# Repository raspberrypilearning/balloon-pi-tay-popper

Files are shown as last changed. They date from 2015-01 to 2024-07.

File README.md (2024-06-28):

# Balloon Pi-tay popper

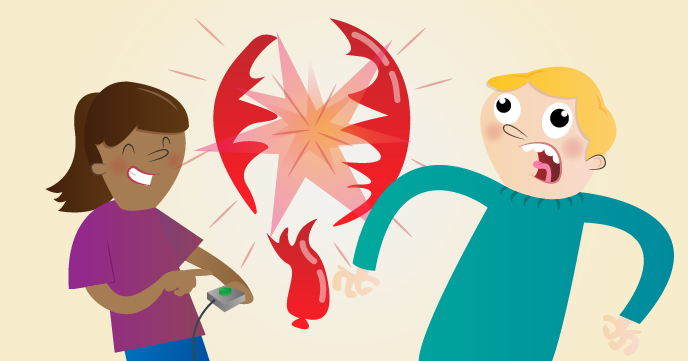
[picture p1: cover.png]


To pop balloons you might usually use a pin. Here you’ll be doing the same, but using a GPIO pin on your Raspberry Pi, not the pin you might be thinking of!

## Requirements

As well as a Raspberry Pi with an SD card loaded with Raspbian, you'll also need:

### Hardware

- 1 x Solderless breadboard
- 4 x Pin-to-socket jumper leads
- 7 x Pin-to-pin jumper leads
- 1 x Push-to-make switch
- 1 x Battery snap
- 2 x 4m core speaker cable (bell wire)
- Some 12R resistors
- 2 x BC635 transistors

### Extras

- Red electrical tape
- Black electrical tape
- String
- Balloons
- 9 volt battery
- Wire strippers or scissors

## The worksheet

- [Worksheet](worksheet.md)

## Licence

Unless otherwise specified, everything in this repository is covered by the following licence:



***Balloon Pi-tay popper*** by [Fran Scott](https://github.com/franscott) and the [Raspberry Pi Foundation](http://www.raspberrypi.org) is licensed under a [Creative Commons Attribution 4.0 International Licence](http://creativecommons.org/licenses/by-sa/4.0/).

Based on a work at https://github.com/raspberrypilearning/balloon-pi-tay-popper

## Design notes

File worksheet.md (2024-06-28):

# Balloon Pi-tay popper

To pop balloons you might usually use a pin. Here you'll be doing the same, but using a GPIO pin on your Raspberry Pi, not the pin you might be thinking of!

## Wire up a button

First, we'll wire our push button up to the Raspberry Pi.

1. Take a pin-to-socket jumper cable and connect the Raspberry Pi's ground pin to the breadboard to make a ground rail:

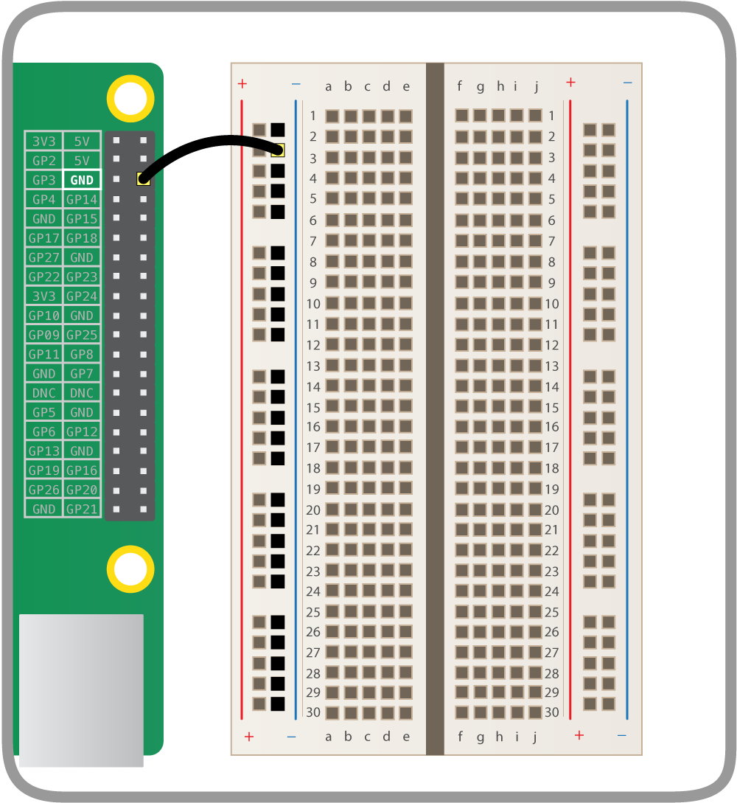
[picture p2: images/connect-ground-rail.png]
    

1. Place the push button on the breadboard and connect one of its legs to the ground rail, and one to GPIO 14:

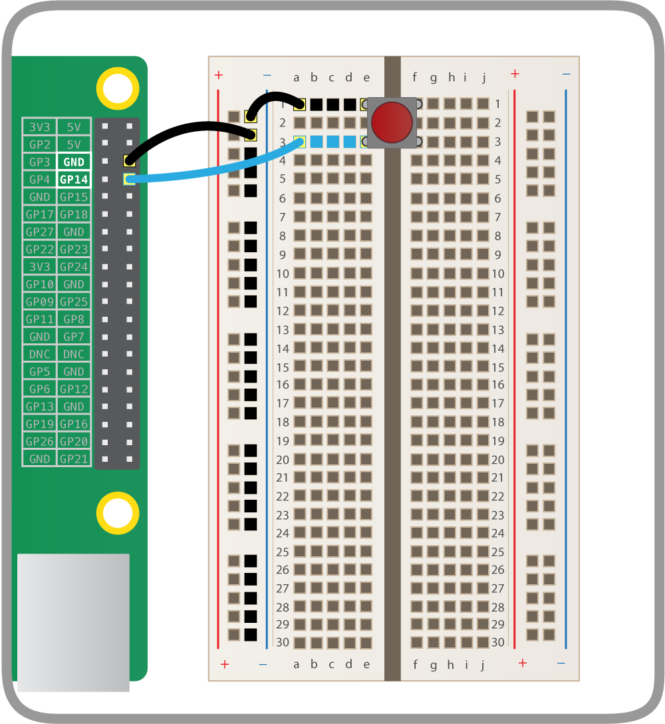
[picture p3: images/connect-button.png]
    

## Test the button with code

Now we've connected a button, we'll activate it with some Python code.

1. Open IDLE by clicking on **Menu** > **Programming** > **Python 3 (IDLE)** to open a Python shell.

1. In this shell, go to `File -> New File` to open a new Python file.

1. It's good practice to save this file before you type anything important. To save, go to `File -> Save As`, then type in `balloon.py` and click `Save`. Now you can get coding!

1. Start by importing the `gpiozero` library. Write the following line in your Python file:

    ```python
    from gpiozero import Button
    ```

1. Next, leave a new line space to separate your imports from your main code, and add a line to set up a button on pin 14:

    ```python
    button = Button(14)
    ```

1. Now add the following lines:

    ```python
    print("Ready...")
    button.wait_for_press()
    print("Pop!")
    ```

    This will print "Ready", wait for the button to be pressed, and then print "Pop!" which will be the point when our balloon pops later!

1. Save the code with `Ctrl + S` and run with `F5`. When you see `Ready...` on the screen, press the button, and you should see `Pop!` printed to the screen.

## Set up the balloon popper

We're going to be using a resistor to make the balloon pop. Resistors are electrical components which reduce the current flowing around a circuit, and in doing so they sometimes get hot. You're going to be taking advantage of this heat and deliberately overheating a resistor in order to pop a balloon. Before you can do that, though, you need to wire up the resistor:

1. Inflate a balloon so it's nice and full, then tie a knot in it.

1. Take 2 meters of 2-core speaker cable and strip both ends of both cores so that the bare wire is visible: strip 1 cm of insulation off one end (the end we'll connect to the breadboard) and about 3 cm off the other end (the end we'll connect to the 12Ω resistor). This can be done with wire strippers or, if you're very careful, with scissors - make sure that you only cut through the insulation and not the wires themselves. You can also split the two cores of the cable a little by simply pulling them apart.

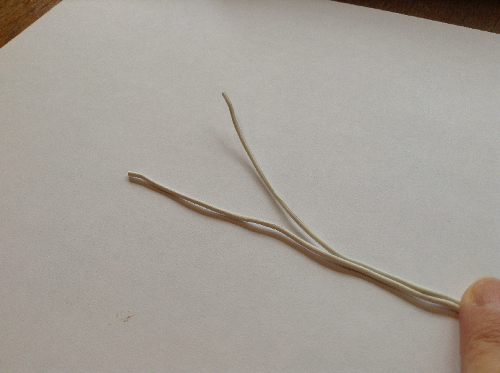
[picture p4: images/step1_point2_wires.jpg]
    

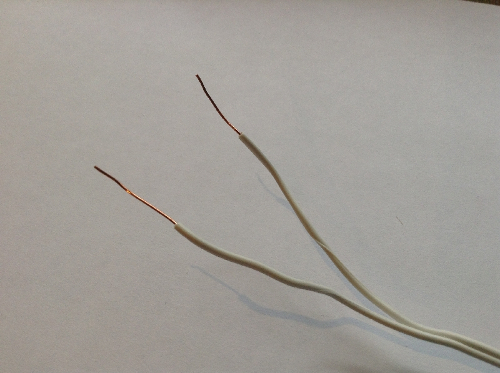
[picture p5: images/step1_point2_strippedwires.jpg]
    

1. Take a 12Ω resistor and the 3 cm stripped end of the speaker cable. Twist one wire of the cable around one wire coming from the resistor, and the other wire around the other wire coming from the resistor; it doesn't matter which wire is connected to which, just make sure the two ends of the wire do not touch each other.

    Make sure that there's a firm connection; you can even wrap electrical tape around the twisted wire to ensure it stays in place.

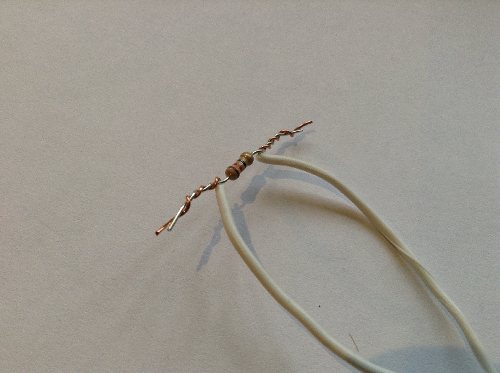
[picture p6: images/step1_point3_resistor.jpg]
    

1. Now, take some more electrical tape (it doesn't matter what colour you use) and tape the resistor firmly onto the most stretched part of the balloon; that's the balloon's side, as in the picture below. It's important that this resistor is firmly touching the balloon, so stick it on carefully.

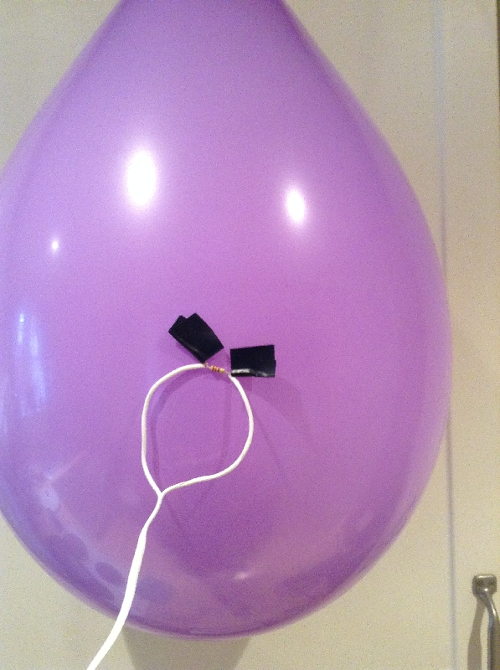
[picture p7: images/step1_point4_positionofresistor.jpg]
    

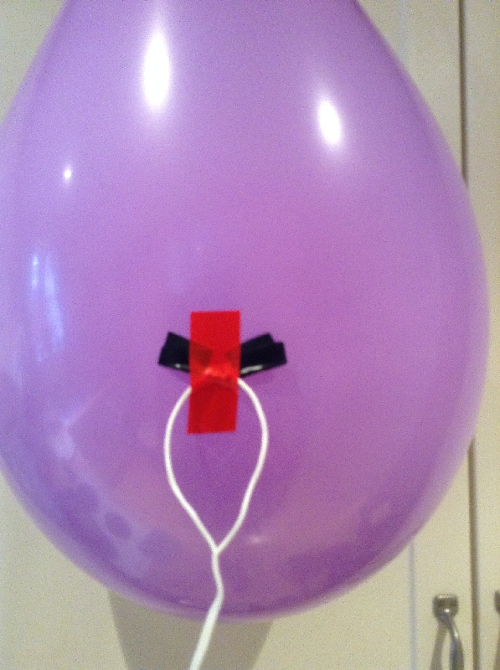
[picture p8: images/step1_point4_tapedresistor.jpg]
    

1. Now tie some string onto the knot of your balloon and hang it from the ceiling using tape or Blu-Tack.

## Connect the transistor

The voltage of a circuit is the amount of 'push' the current has: a higher voltage provides a bigger push, which usually results in more current flowing in the circuit. Here, in order to make the resistor hot enough to pop the balloon, we need to run a higher current through them than the voltage on the Raspberry Pi can provide, and to do this we'll use a device called a transistor.

A transistor allows you to 'amplify' a circuit, as they can be switched 'on' by a low-voltage circuit, and once 'on' they allow a higher-voltage circuit to flow. However, it's important that they're wired up correctly.

Hold your transistor up and you'll see that it's a semi-circular shape, with three leads coming out the bottom. Each of these leads has a different name and role.

The base controls the transistor and if it receives a signal (a small voltage) it turns the transistor 'on', allowing current from a higher-voltage circuit to flow between the collector and the emitter.

** Please note: some models of transistors have the legs in a different order. If you're not using BC635 transistors then you must look at the datasheet to check that your wiring is correct. Incorrect wiring could damage your Pi or the transistor, or make your balloon pop too early!**

Hold the BC635 transistor with the flat side facing towards you: from left to right the leads are called the emitter, the collector, and the base.

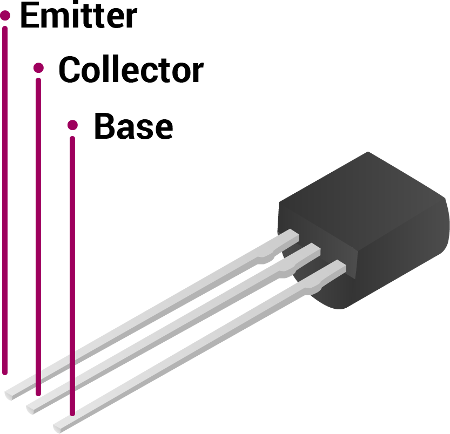
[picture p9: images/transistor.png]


1. Carefully place the transistor onto the breadboard, with the flat side facing the ground rail and a 330Ω resistor connected to the base, like so:

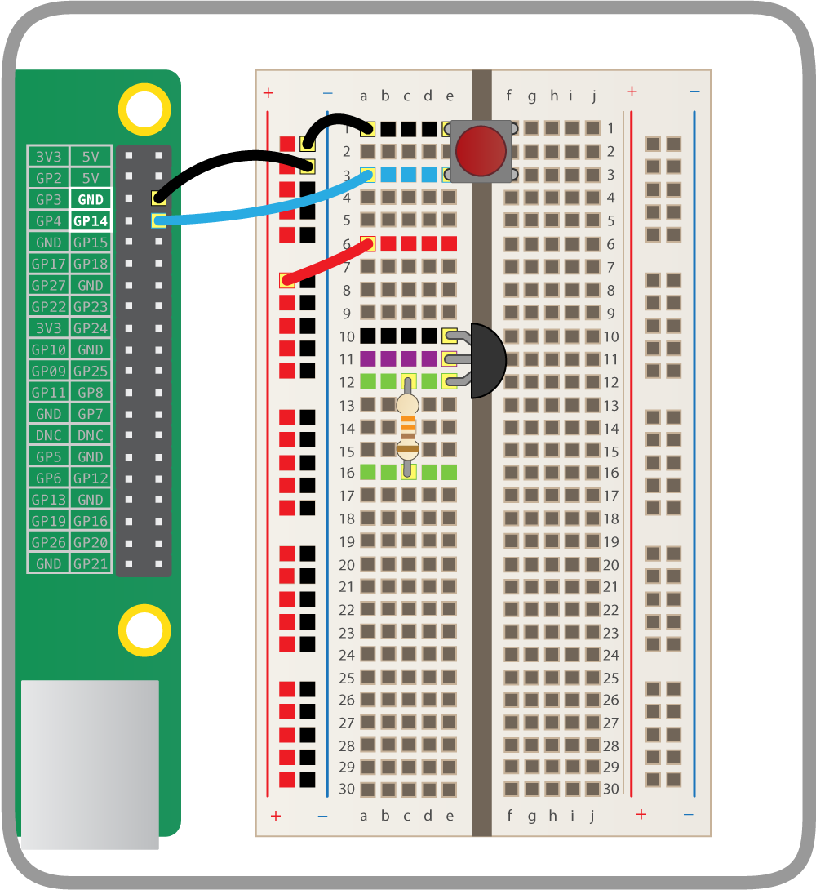
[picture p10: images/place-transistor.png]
    

    Be sure to place one leg in each hole in the same row.

1. Now connect the top leg of the transistor to the ground rail, and the bottom leg of the 330Ω resistor to GPIO 2 on the Raspberry Pi:

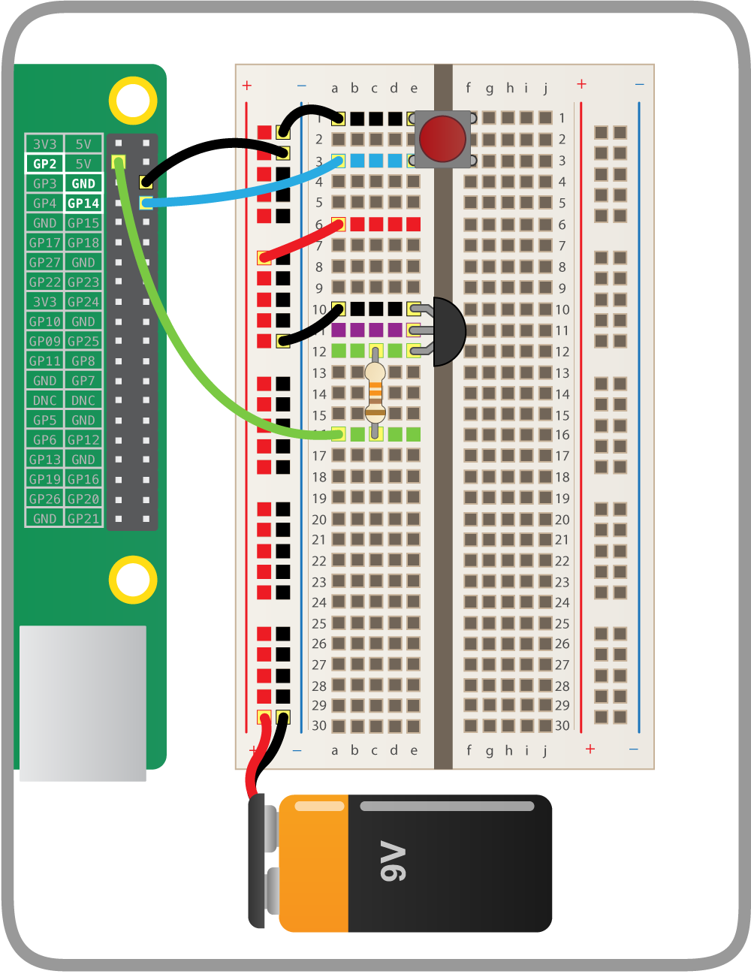
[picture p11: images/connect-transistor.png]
    

## Connect the balloon

Now we're going to use a 9V battery. We need 9 volts for the resistor to get hot enough to pop the balloon!

1. Place the battery in the battery snap. Connect its black lead into the ground rail and the red lead into the power rail on your breadboard - that's the red one adjacent to the ground rail.

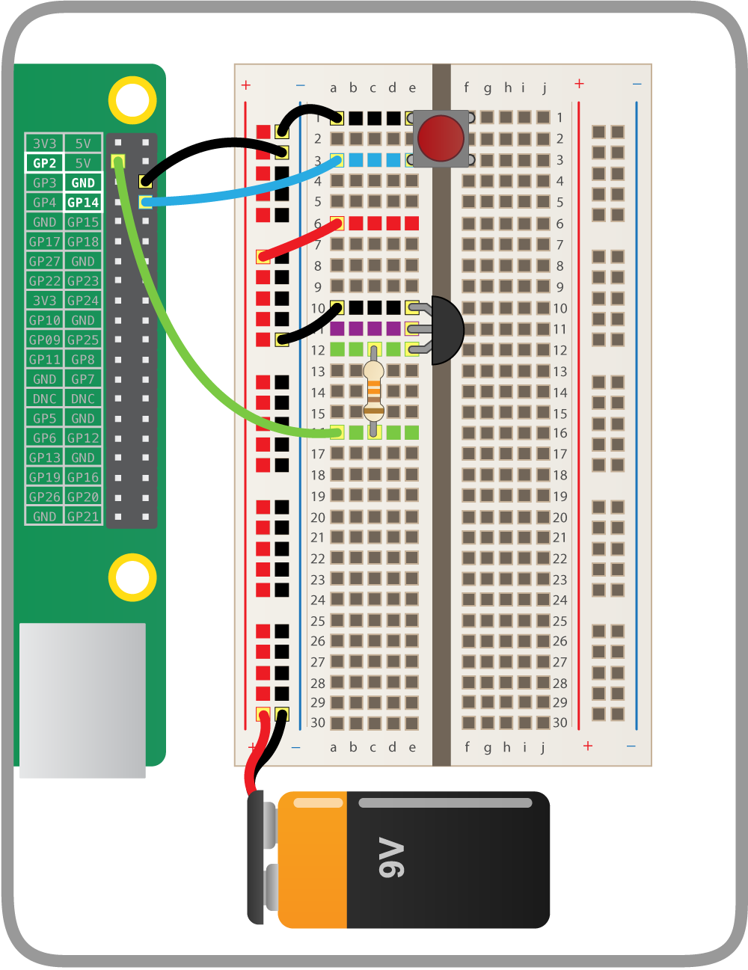
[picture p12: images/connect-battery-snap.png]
    

1. We want this circuit to go through the resistor attached to the balloon. Connect it to the breadboard in the space between the button and the transistor:

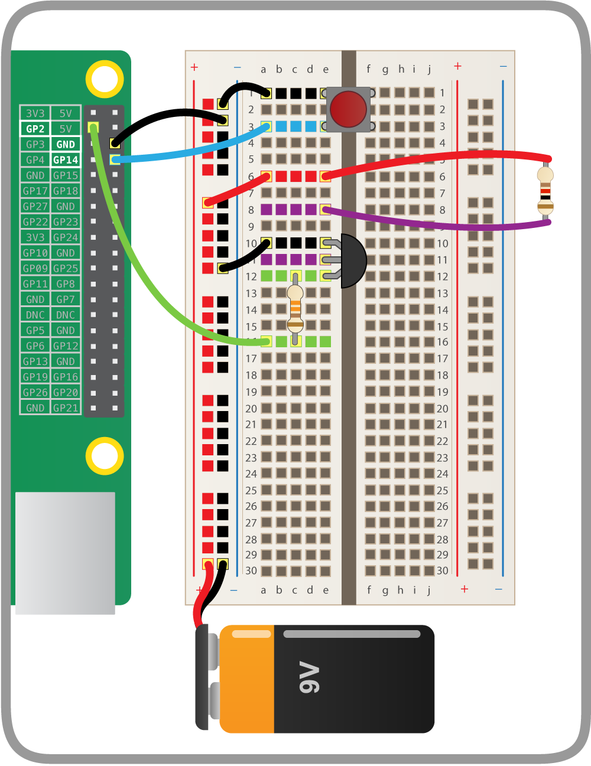
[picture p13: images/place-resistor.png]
    

1. Now connect one side of the resistor to the middle leg of the transistor, and the other side to the 9V power rail:

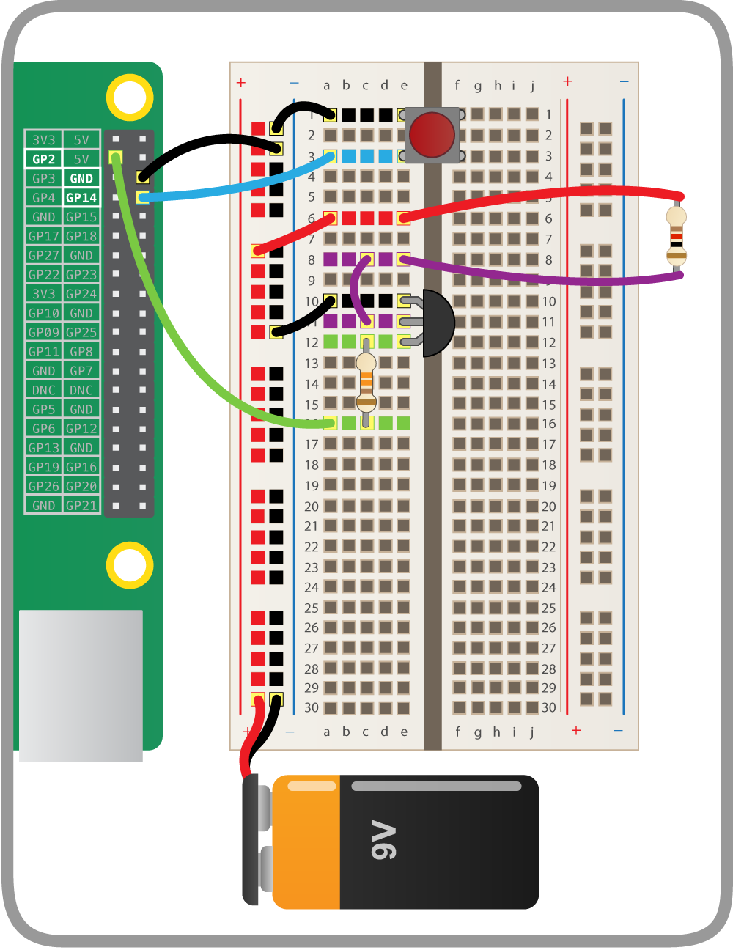
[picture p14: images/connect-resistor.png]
    

    This circuit is now complete. The current will flow from the battery, through the resistor to the collector leg of the transistor, out the emitter leg and then back to ground. As the current flows through the resistor, it will heat it up so much that the balloon will pop.

## Add the balloon to the code

Now we've completed our circuit we'll need to change our code to trigger the transistor, allowing current to flow through the resistor, which will pop the balloon.

1. First, you're going to need an `OutputDevice` to trigger the transistor, and you'll need the `sleep` method from the `time` library.  Add `OutputDevice` and import the `sleep` method at the beginning of your code:

    ```python
	from gpiozero import Button, OutputDevice
	from time import sleep
	```

1. Where you previously declared `button = 14`, add a line to declare `balloon = 2`:

    ```python
    button = Button(14)
    balloon = OutputDevice(2)
    ```

   This will designate GPIO 2 as what we'll use to pop the balloon.

1. Now comes the code to pop the balloon. Earlier, we used `button.wait_for_press()` to wait for a button press, then we just printed `Pop!`. Add the following lines before the `Pop!` line:

    ```python
    balloon.on()
    sleep(10)
    balloon.off()
    ```

    This means "Turn the balloon pin on for 10 seconds, then turn it off".
    
    Depending on the thickness of your balloon and how much it has been blown up and stretched, this may take five seconds or more. If your balloon does not pop, you can increase the length of the `sleep` time accordingly.

1. Now save your code with `Ctrl + S`, check everything's wired up as it should be, then run your code with `F5`. When you see `Ready...`, press the button and your balloon should burst!

## Set up more balloons

Popping one balloon is good, but popping more balloons is so much better! For each extra balloon you'll need another transistor, another resistor, three pin-to-pin jumpers, one pin-to-socket jumper, and space on your breadboard.

1. Set up the first balloon as before, replacing the old resistor (it's now burned out!). Leave the rest of the cabling as it is.

1. Set up a second balloon with another resistor.

1. Add your second transistor to the breadboard and wire it up in the same way as before. Connect the inside leg to the ground rail and its outside leg to GPIO 3 through a 330Ω resistor (leave the middle leg for now):

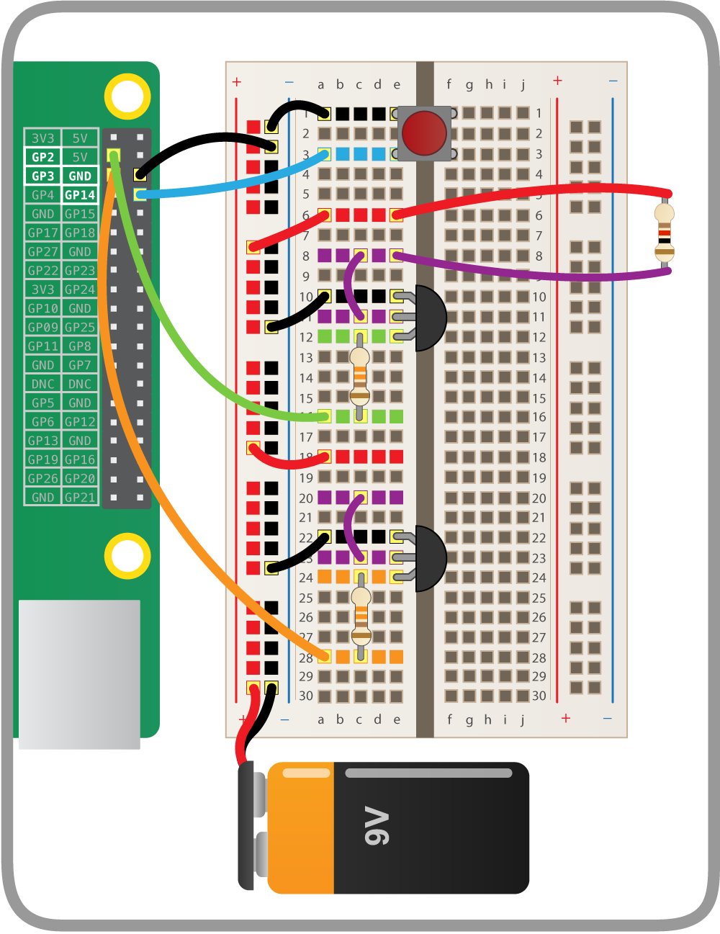
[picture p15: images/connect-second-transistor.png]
    

1. Now connect the second transistor to the second balloon's resistor:

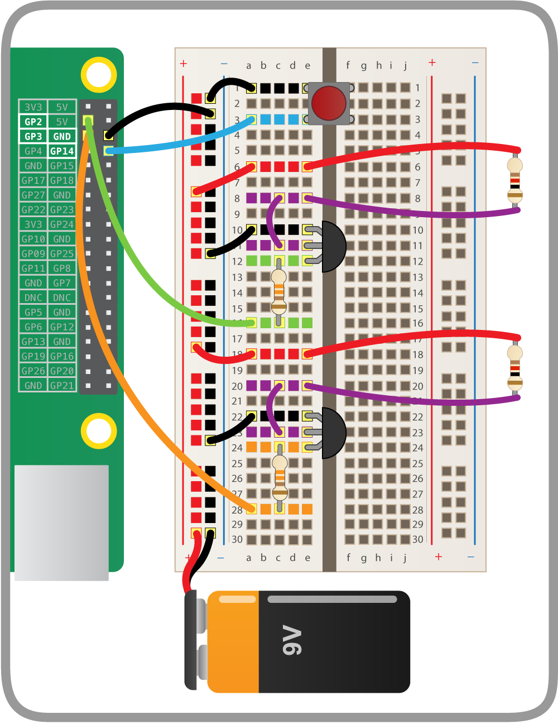
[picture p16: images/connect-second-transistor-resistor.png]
    

    That's it for the wiring, but you can add more balloons if you like!

## Code more balloons

Now we'll return to the code and make a few small adjustments to make it pop more balloons!

1. Where we previously used `balloon = OutputDevice(2)` to store the GPIO pin for the first balloon, you'll now need to set up more balloons. You can do this using a list:

    ```python
	balloons = [OutputDevice(2), OutputDevice(3)]
    ```

1. Then, instead of just popping one balloon, we'll make it pop them all in turn:

    ```python
    for balloon in balloons:
        print("Armed...")
		balloon.on()
        sleep(10)
		balloon.off()
    ```

## What next?

Other stuff to try:

- Try changing the balloons' popping order. To do this, just change the order in which the GPIO pin numbers are used.

- Why not try to have the balloons pop when a motion sensor is triggered? You can find out how to use a motion sensor in the [parent detector resource](https://www.raspberrypi.org/learning/parent-detector/).

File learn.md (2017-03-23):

By creating a balloon-popping circuit with your Raspberry Pi you will learn:

- How to wire up a circuit
- What transistors are used for
- How to use a push button to control current
- How to use Python code to control the Pi's GPIO pins, to heat up a resistor enough to pop a balloon!

This resource covers elements from the following strands of the [Raspberry Pi Digital Making Curriculum](https://www.raspberrypi.org/curriculum/):

- [Use basic programming constructs to create simple programs](https://www.raspberrypi.org/curriculum/programming/creator)
- [Combine inputs and/or outputs to create projects or solve a problem](https://www.raspberrypi.org/curriculum/physical-computing/builder)
- [Use basic materials and tools to create project prototypes](https://www.raspberrypi.org/curriculum/manufacture/creator)

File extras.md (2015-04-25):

You'll also need:

- Electrical tape (in black and red)
- String
- Balloons
- Wire strippers or scissors

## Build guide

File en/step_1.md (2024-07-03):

## What you will make

<html>
<video width="540" height="720" controls>
<source src="images/balloon popper.mp4" type="video/mp4">
Your browser does not support the video tag.
</video>
</html>

--- collapse ---

---

title: Safety note

---

In this project, you will heat a 12Ω resistor so that it pops a balloon.

- Do not touch the resistor when the circuit is triggered. It will get VERY hot.
- The transistor may also get hot.
- The balloon will make a loud noise when it pops, which may be distressing for some people.

--- /collapse ---

--- collapse ---

---

title: What you will need

---
* 1 x Solderless breadboard
* 1 x 9V battery
* 1 x Battery snap
* 1 x Tactile button
  
For each balloon:
* 4 x pin-to-pin jumper leads
* 3 x pin-to-socket jumper leads
* 1 x 2m strip of 2-core speaker cable
* 1 x 12Ω resistor
* 1 x 330Ω resistor
* 1 x BC635 transistor

--- /collapse ---

--- collapse ---

---

title: What you will learn

---
- How to wire up a circuit
- What transistors are used for
- How to use a push button to control current
- How to use Python code to control the Pi's GPIO pins, to heat up a resistor enough to pop a balloon!

--- /collapse ---

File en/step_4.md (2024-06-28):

## Set up the balloon popper

We're going to be using a resistor to make the balloon pop.

--- collapse ---

---

title: What are resistors

---

Resistors are electrical components which reduce the current flowing around a circuit, and in doing so they sometimes get hot. You're going to be taking advantage of this heat and deliberately overheating a resistor in order to pop a balloon.

--- /collapse ---

--- task ---

Inflate a balloon so it's nice and full, then tie a knot in it.

--- /task ---

--- task ---

Take two wires, each about 2 meters in length and strip both ends, so the bare wires is visible.

2-core speaker cable

2-core speaker cable, with stripped ends

--- /task ---

--- task ---

Take a 12Ω resistor and the stripped end of the wire. Twist one wire of the cable around one leg coming from the resistor, and the other wire around the other leg coming from the resistor; it doesn't matter which wire is connected to which, just make sure the two ends of the wire do not touch each other.

Make sure that there's a firm connection; you can even wrap electrical tape around the twisted wire to ensure it stays in place.

A resistor secured to speaker cable

--- /task ---

--- task ---

Take some more electrical tape (it doesn't matter what colour you use) and tape the resistor firmly onto the most stretched part of the balloon; that's the balloon's side, as in the picture below. It's important that this resistor is firmly touching the balloon, so stick it on carefully.

A resistor secured to the side of a balloon

The resistor secured with even more tape!

Now tie some string onto the knot of your balloon and hang it from the ceiling using tape or Blu-Tack.

--- /task ---

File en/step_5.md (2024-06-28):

## Connect the transistor

--- collapse ---

---

title: Transistors

---

The voltage of a circuit is the amount of 'push' the current has: a higher voltage provides a bigger push, which usually results in more current flowing in the circuit. Here, in order to make the resistor hot enough to pop the balloon, we need to run a higher current through them than the voltage on the Raspberry Pi can provide, and to do this we'll use a device called a transistor.

A transistor allows you to 'amplify' a circuit, as they can be switched 'on' by a low-voltage circuit, and once 'on' they allow a higher-voltage circuit to flow. However, it's important that they're wired up correctly.

Hold your transistor up and you'll see that it's a semi-circular shape, with three pins coming out the bottom. Each of these pins has a different name and role.

The base controls the transistor and if it receives a signal (a small voltage) it turns the transistor 'on', allowing current from a higher-voltage circuit to flow between the collector and the emitter.

** Please note: some models of transistors have the pins in a different order. If you're not using BC635 transistors then you must look at the datasheet to check that your wiring is correct. Incorrect wiring could damage your micro:bit or the transistor, or make your balloon pop too early!**

--- /collapse ---

--- task ---

Hold the BC635 transistor with the flat side facing towards you: from left to right the pins are called the emitter, the collector, and the base.

A labelled diagram of a BC635 transistor

--- /task ---

--- task ---

Carefully place the transistor onto the breadboard, with the flat side facing the ground rail and a 330Ω resistor connected to the base, like so:

The components in the breadboard

Be sure to place one pin in each hole in the same row.

--- /task ---

--- task ---

Now connect the emitter to the ground rail, and the unconnected end of the 330Ω resistor to GPIO 2 on the Raspberry Pi:



--- /task ---

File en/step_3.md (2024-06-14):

## Test the button with code

Now we've connected a button, we'll activate it with some Python code.

--- task ---

Open Thonny by clicking on **Menu** > **Programming** > **Thonny**

--- /task ---

--- task ---

To save, go to `File -> Save As`, then type in `balloon.py` and click `Save`. Now you can get coding!

--- /task ---

--- task ---

Start by importing the `gpiozero` library. Write the following line in your Python file:

```python
from gpiozero import Button
```

--- /task ---

--- task ---

Next, leave a new line space to separate your imports from your main code, and add a line to set up a button on pin 14:

```python
button = Button(14)
```

--- /task ---

--- task ---

Now add the following lines:

```python
print("Ready...")
button.wait_for_press()
print("Pop!")
```

This will print "Ready", wait for the button to be pressed, and then print "Pop!" which will be the point when our balloon pops later!

Click **Run** to see `Pop!` being printed.
--- /task ---

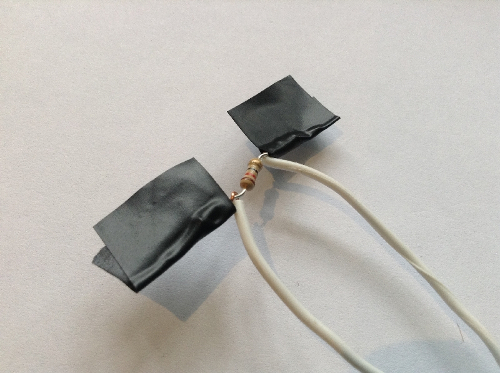
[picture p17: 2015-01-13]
en/images/step1_point3_tapedresistor.jpg

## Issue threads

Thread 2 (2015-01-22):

Transistor spec important, and needs a current limiting resistor in the base!

jimbojr, 2015-01-22:
The base of the transistor is connected directly to a GPIO pin which is not good and may damage the Pi – basically it is just shorting the GPIO to GND via a diode, a current imiting resistor of 330R is needed.

Also the resource should mandate the type of transistor not merely suggest it as it needs to sink 750mA. The BC635 is fine as it can cope with 1A  but a lot of common SS variants will not – and may be destroyed in interesting ways (explode, overheat or catch on fire) which may be fun for the kids anyway but….

RZRZR, 2015-01-27:
Thank you

MarcScott, 2016-06-09:
@samalderhyde
Could you redo this image for me:
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
so that the base of the transistor (the lowest leg on the diagram) connects to a 330ohm resistor (orange orange brown) and then that then connects to GPIO2, as shown below:
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
All other components can remain the same

Closed 2016-06-14.

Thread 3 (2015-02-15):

Remove lightly coloured wires

gbaman, 2015-02-15:
Used this activity at the Northern Ireland Raspberry Jam today. All our worksheets are printed out black and white half way through the activity I noticed, the yellow wire on the breadboard goes **near completely invisible**.
Caused quite a few issues for the kids doing the activity.

Would be an excellent idea to stay clear of any lightly coloured wires on a white breadboard in the wiring diagrams, as I am sure I won't be the only one printing the activity out in black and white.

LizUpton, 2015-02-15:
Thanks @gbaman. Sam's on vacation this week, but I'll talk to him about it next week: it may be worth outlining paler wires in black for this reason. Thanks very much for the spot!

bennuttall, 2015-06-19:
Thanks - will bear in mind.

Closing as this is issue is not specific to this resource.

Closed 2015-06-19.

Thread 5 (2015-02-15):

Speaker wire not needed

gbaman, 2015-02-15:
At today's NI Raspberry Jam, we just used normal single core wire for the activity as we weren't able to cheaply (speaker wire is pretty expensive) source decent amount of speaker wire. The activity worked perfectly fine.
It easily allowed more than enough current to pop the balloons.
Any reason speaker wire is recommended? May at least be worth mentioning normal wire can be used as well in the parts list for those without decent budget?
It is £12 per balloon wired up with the Maplin sourced speaker wire.

bennuttall, 2015-02-24:
We thought the speaker wire was cheaper, but you're right, we'll change it to core wire.

Can you recommend a place to buy? A link would be handy :)

gbaman, 2015-02-24:
An excellent question.
Pimoroni stick a hookup wire kit - http://shop.pimoroni.com/products/hook-up-wire-spool-set
Although it is a little pricey. Might be able to get away with this, not certain though - http://www.maplin.co.uk/p/bell-cable-single-core-priced-per-metre-xs92a

bennuttall, 2015-02-24:
That looks better (I'm sure we had that in at one point).

So Maplin's [bell cable](http://www.maplin.co.uk/p/bell-cable-single-core-priced-per-metre-xs92a) is 69p per metre compared to their [speaker wire](http://www.maplin.co.uk/p/speaker-cable-figure-of-8-6-x-3mm-white-priced-per-metre-xr60q) at £1.59 per metre.

@RZRZR sound good? Shall I update it?

RZRZR, 2015-02-24:
The pimoroni wire would work out about £11.88 worth for three balloon too - because you'd need twice as much as it's single core.

We went for bell wire because it's easy to pick up at any length, has nice thick core and is conveniently 2-core. Yes @bennuttall, it was bell cable originally - must have got lost in the confusion - let's change it back.

Closed 2015-02-24.

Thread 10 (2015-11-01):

Balloon pops without code

brijrajsingh, 2015-11-01:
Please see my attached diagram, I am using your code and identical connections, the "pop" msg printing with tactile switch works just fine, but when i do the full implementation, i find that the balloon pops the moment i input the battery.
I later started checking with LED, there is no effect over the LED, neither it gets hot or turns off by the code given, the code doesn't show any error as well

I however see this warning in my console

balloon_updated.py:13: RuntimeWarning: A physical pull up resistor is fitted on this channel!
  GPIO.setup(balloon, GPIO.OUT)
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

juggledad, 2015-11-01:
Make sure you transistor is in the correct way. Some transistors have the EBC in a different order.

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

brijrajsingh, 2015-11-02:
Should I just revert it in such a case, So if its the other way around it should work, I just hope I don't end up burning my pi.

juggledad, 2015-11-02:
You need to look at the data sheet for the transistor from the company that makes it (google it) to see the correct layout.

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

brijrajsingh, 2015-11-04:
yes, Found that my transistor had order EBC unlike yours, the code works like a charm

Closed 2015-11-04.

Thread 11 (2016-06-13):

copy edit

MarcScott, 2016-06-13:
Hi @lauraclay / @LornaLynch
Could I get a copy edit on this update please:
New fork is at - https://github.com/raspberrypilearning/balloon-pi-tay-popper/tree/gpiozero-update
Comparison of new and original at - https://github.com/raspberrypilearning/balloon-pi-tay-popper/compare/gpiozero-update?expand=1

I've changed some diagrams and updated the copy and code for gpiozero
Not too many changes

Thanks

LornaLynch, 2016-06-13:
Is it a problem that, in the section where the speaker cable/resistor circuit is being prepared, there's no red or black electrical tape on the cables, though this is mentioned in the worksheet?

MarcScott, 2016-06-13:
It's not a massive issue. I'll take some new photos when I'm back in the office. Good spot though.

LornaLynch, 2016-06-13:
Final one from me, and then the edit is done: I'd say the interactive calculator suggestion in what next might need a tiny bit of explanation? Is there something that could be linked to?

LornaLynch, 2016-06-13:
Other than this I'd say you're ok to close this issue.

MarcScott, 2016-06-13:
Thanks @LornaLynch

MarcScott, 2016-06-13:
@davidhoness was this your resource originally? Could you clarify the interactive calculator suggestion at the end.

bennuttall, 2016-06-13:
It was an external one, rewritten by me & Rachel. I'll take a look.

lauraclay, 2016-06-15:
Reopening, as I've spotted some further edits are needed. (Apologies for just seeing this- problems migrating my email meant I've missed a week of notifications!)

LornaLynch, 2016-06-15:
Apologies @lauraclay :(

Closed 2017-02-24.

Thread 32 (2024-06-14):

There was an issue saving the file: #balloo_zero.py#

raspberrypilearningbot, 2024-06-14:
#balloo_zero.py# from https://raw.githubusercontent.com/raspberrypilearning/balloon-pi-tay-popper/6e53bd7cd69007b8f373cac3a6fe468957bee8e9/en/resources/%23balloo_zero.py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 in en. Error: 404 Not Found

Closed 2024-06-14.

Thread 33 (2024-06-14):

en/solutions missing

raspberrypilearningbot, 2024-06-14:
Expected a file or directory at en/solutions

Closed 2024-06-14.

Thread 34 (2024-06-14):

en/step_10.md missing

raspberrypilearningbot, 2024-06-14:
Expected a file or directory at en/step_10.md

Closed 2024-06-14.

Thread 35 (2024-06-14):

en/step_11.md missing

raspberrypilearningbot, 2024-06-14:
Expected a file or directory at en/step_11.md

Closed 2024-06-14.

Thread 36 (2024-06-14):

Unable to process Set up more balloons content

raspberrypilearningbot, 2024-06-14:
There is a markdown issue in step Set up more balloons in locale: en. Error: Markdown contained an unclosed tag: ["task"]

For `mapping values are not allowed in this context` errors, the reported line number may be misleading (due to https://github.com/ruby/psych/issues/190).

Check any YAML (eg. in your `---code---` blocks) as missing colons, or a missing space after a colon, are common issues.

Try pasting the YAML into this linter if you're stuck: http://www.yamllint.com/

Closed 2024-06-14.

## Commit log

2015-01-13 Copy in contents from Fran, add meta files
    [hardware.yml]
2015-01-13 Update circuit diagrams
2015-01-15 Change switch to tactile button
    [hardware.yml]
2015-01-19 hardware requirement changes
    [hardware.yml]
2015-01-19 Correct transistor legs
2015-01-19 Correct reference to push button component image
    [hardware.yml]
2015-01-19 Update tactile button link
    [hardware.yml]
2015-01-19 Update number of jumpers required
    [hardware.yml]
2015-02-24 Replace speaker wire with bell wire, close #5
    [hardware.yml]
2015-02-24 Add 9V battery
    [hardware.yml]
2015-02-24 Remove 9V battery
    (it's now in hardware)
2015-03-12 Update reference to specific resistor
    [hardware.yml]
2015-03-13 Swap order of wire images
2015-08-07 Update push button url
    [hardware.yml]
2016-03-22 Remove URLs from harware.yml
    [hardware.yml]
2016-06-13 updated images and text for safe transistor use
    - Added 330Ω resistor to base of transistors
    - Updated text to reflect changes
    [hardware.yml, sketch.fzz]
2016-06-14 updated wiring diagrams, close #2
2016-06-15 Copy edit
    [hardware.yml]
2016-06-15 Copy edit
    In the Hardware list, it specifies bell wire, but this isn't mentioned again, and this worksheet suggests using 2 core speaker cable. I'm aware that bell wire is cheaper, but speaker cable is possibl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
2016-09-09 Change 'bell wire' to '2-core speaker cable'
    Think this was mentioned when this resource was first edited, but bell wire is only mentioned in this list; the worksheet mentions 2-core speaker cable instead, so I'm changing this list. If it was i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
    [hardware.yml]
2017-06-11 Fix missing images in requirements
    [hardware.yml]
2017-06-11 Correct connection of GPIO2 to resistor, not transistor
2017-06-11 Different instructions for stripping the 2-core wire
    There's no need to label the ends of the wire with red and black electrical tape, plus it's additional resources that you don't really need to complete the worksheet.
2017-06-17 Change GPIO pin X to GPIO X
2017-07-25 Automated content import
    [sketch.fzz]
2024-06-28 removed gendered language
    [hardware.yml]
